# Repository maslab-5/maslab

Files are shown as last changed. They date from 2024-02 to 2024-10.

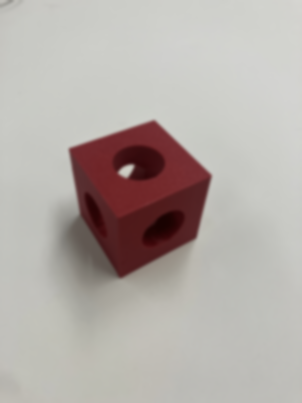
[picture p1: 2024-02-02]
nuc/vision/img/blur.png

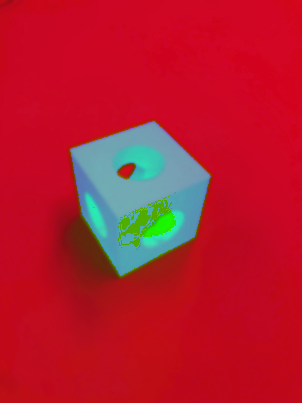
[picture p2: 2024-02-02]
nuc/vision/img/hsv.png

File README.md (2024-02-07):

# MASLAB Robot
MIT Mobile Autonomous Systems Laboratory (MASLAB) Robotics Competition – Team 5 [\[website\]](https://maslab.mit.edu/2024/wiki/team05)
<br>
Monolithic repository containing all codes and files: cad, pcb, stm32 (c), nuc (python/cv), web
<br>
<br>
1st place winner of the 2024 competition, held during IAP on February 2nd. 
<br>
Developed by Miguel Flores-Acton, Anshul Gupta, and Andy Yu

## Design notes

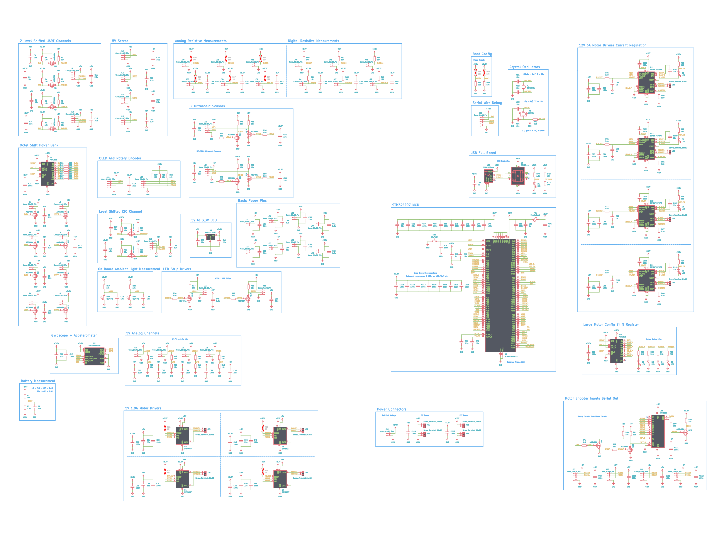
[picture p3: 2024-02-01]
web/resources/Jan_1-2/Schematic.png

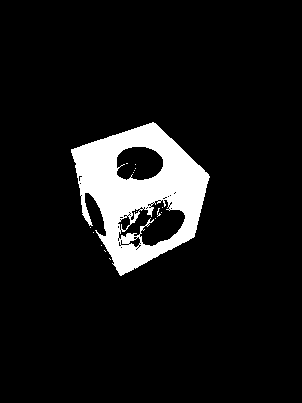
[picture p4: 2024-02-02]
nuc/vision/img/cmask.png

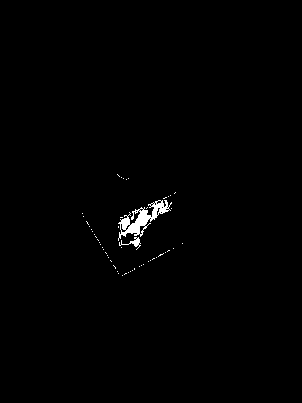
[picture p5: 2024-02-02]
nuc/vision/img/mask1.png

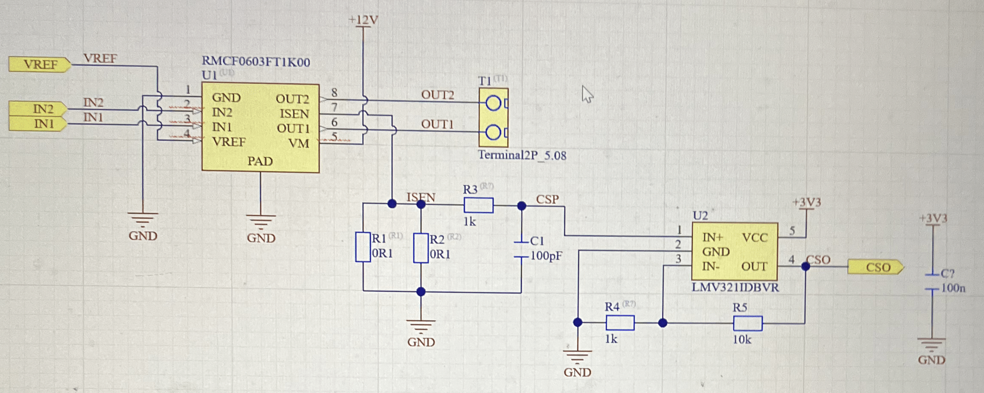
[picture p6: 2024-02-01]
web/resources/Dec_27-31/Altium.png

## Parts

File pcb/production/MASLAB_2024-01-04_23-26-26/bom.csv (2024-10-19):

Designator | Footprint | Quantity | Value | LCSC Part #
C10, C11, C14, C15, C19, C26, C27, C28, C29, C33, C35, C40, C50, C51, C52, C56, C57, C58, C59, C61, C62, C66, C68, C7, C8, C83, C85, C9 | 0603 | 28 | 2.2u
C100, C101, C102, C103, C104, C105, C110, C111, C112, C113, C114, C115, C12, C120, C121, C2, C20, C21, C22, C30, C31, C32, C34, C38, C43, C44, C48, C49, C71, C73, C74, C76, C80, C81, C84, C86, C88, C89 | 0402 | 38 | 100n
C106, C107, C108, C109, C78, C87, C94, C95 | 0402 | 8 | 1u
C116, C117, C118, C119 | 0402 | 4 | 22n
C13, C69, C77, C96, C97, C98 | C_Elec_8x6.2 | 6 | 100u
C18, C23, C39, C47, C53, C6 | 0402 | 6 | 4.7n
C24, C25, C37, C41, C42, C45, C46 | 0805 | 7 | 22u
C90, C91 | 0402 | 2 | 15p
C92, C93 | 0402 | 2 | 10p
C99 | C_Elec_8x6.2 | 1 | 100u | C178539
D1, D10, D11, D2, D3, D4, D5, D6, D7, D8, D9 | 0603 | 11 | LED
FB1 | 0805 | 1 | FerriteBead
J56 | USB_Micro-B_Molex-105017-0001 | 1 | USB_B_Micro
Q1, Q10, Q11, Q12, Q13, Q14, Q15, Q18, Q19, Q2, Q20, Q21, Q22, Q3, Q4, Q5, Q7, Q9 | SOT-23 | 18 | AO3400A
R1, R10, R11, R12, R23, R24, R27, R28, R30, R31, R32, R35, R37, R39, R43, R45, R5, R51, R52, R53, R54, R55, R62, R63, R64, R65, R66, R67, R7, R74, R75, R82, R83, R9, R97 | 0402 | 35 | 10k
R100, R101, R102, R103, R13, R14, R15, R16, R17, R18, R19, R2, R20, R3, R38, R4, R50, R60, R61, R72, R73, R76, R77, R78, R79, R80, R81, R84, R85, R86, R87, R88, R89, R90, R91, R93, R94, R95, R96, R98, R99 | 0402 | 41 | 510
R29, R36, R42, R44, R46, R47, R6, R8, R92 | 0402 | 9 | 5.1k
SW1 | SW_SPST_TL3342 | 1 | SW_Push
U1, U10 | SOIC-16_3.9x9.9mm_P1.27mm | 2 | 74HC595
U11, U12, U13, U14 | HTSSOP-16-1EP_4.4x5mm_P0.65mm_EP3.4x5mm_Mask2.46x2.31mm | 4 | DRV8874PWPR
U15 | SOIC-16_3.9x9.9mm_P1.27mm | 1 | 74HC165
U2 | LGA-14_3x2.5mm_P0.5mm_LayoutBorder3x4y | 1 | ICM-42670-P
U3, U4, U6, U7 | WSON-8-1EP_2x2mm_P0.5mm_EP0.9x1.6mm | 4 | DRV8837
U5 | SOT-223-3_TabPin2 | 1 | AMS1117-3.3
U8 | LQFP-100_14x14mm_P0.5mm | 1 | STM32F407VETx
U9 | SOT-23-6 | 1 | SRV05-4
Y1 | Crystal_SMD_3215-2Pin_3.2x1.5mm | 1 | 32.768kHz
Y2 | Crystal_SMD_3225-4Pin_3.2x2.5mm | 1 | 16MHz

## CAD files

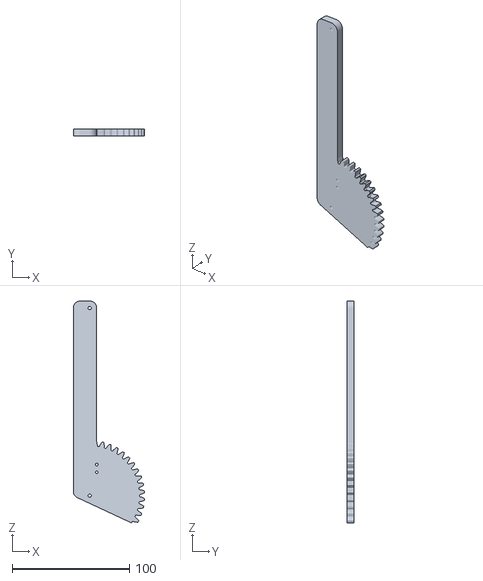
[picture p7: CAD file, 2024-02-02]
cad/parts/GearBar.stl
60.9 x 6.35 x 189.3

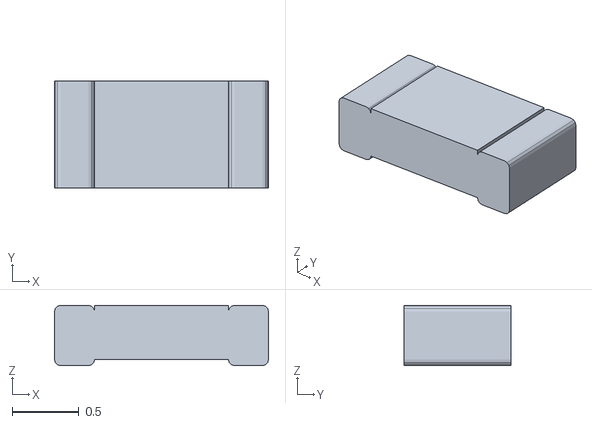
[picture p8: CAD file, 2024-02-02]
cad/parts/SOLID (16).stl
1.60 x 0.8 x 0.45

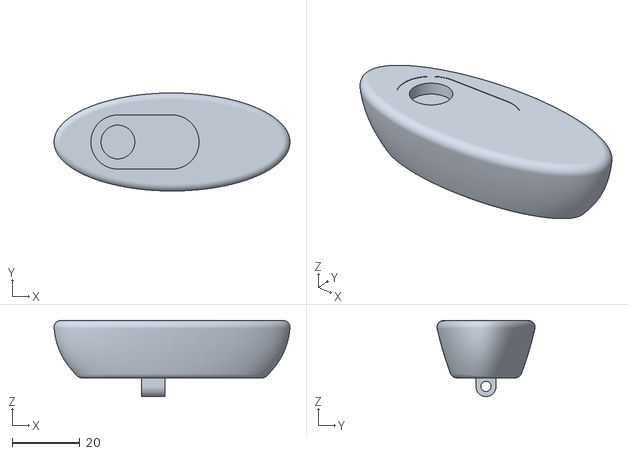
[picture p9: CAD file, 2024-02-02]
cad/parts/Camera.stl
69.8 x 29.0 x 22.5

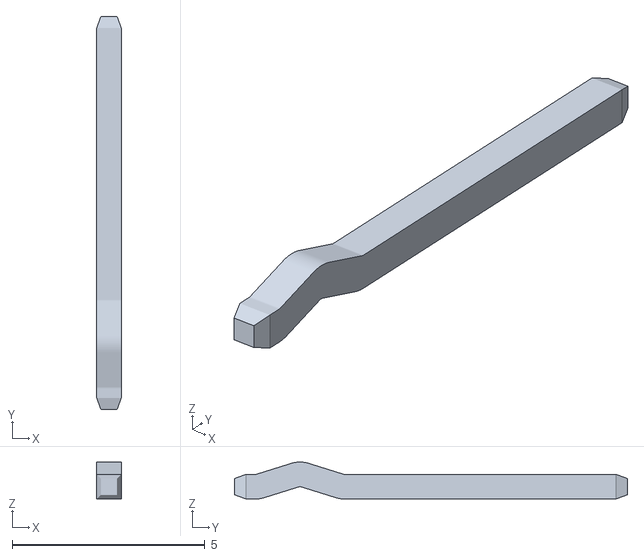
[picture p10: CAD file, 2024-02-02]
cad/parts/COMPOUND (11).stl
0.64 x 10.2 x 0.96

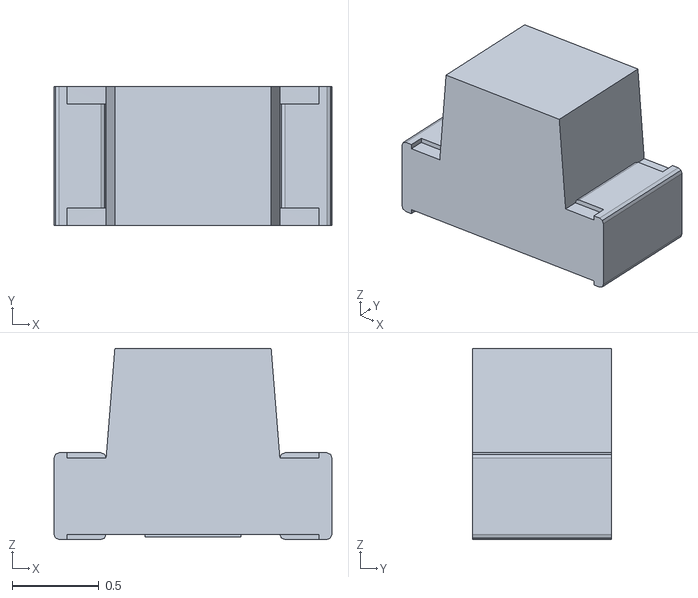
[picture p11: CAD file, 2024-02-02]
cad/parts/SOLID (14).stl
1.60 x 0.8 x 1.10

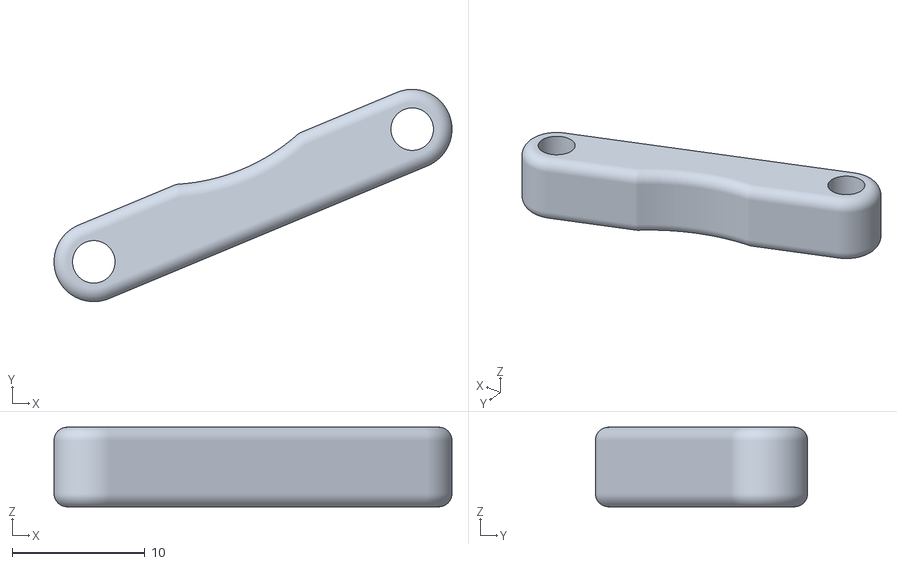
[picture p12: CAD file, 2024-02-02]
cad/parts/FenceLink.stl
30.0 x 16.0 x 6.00

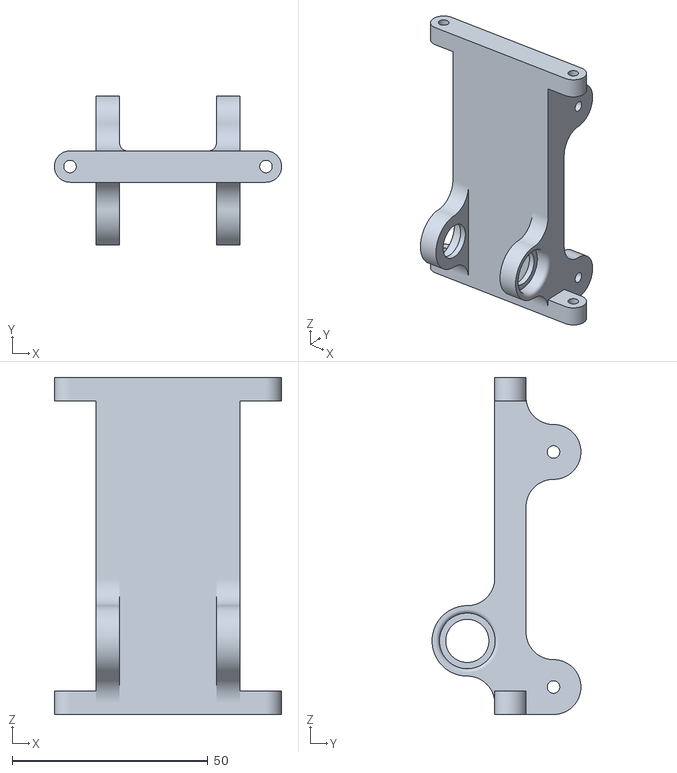
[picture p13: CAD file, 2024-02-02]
cad/parts/BarMount.stl
58.0 x 38.0 x 86.0

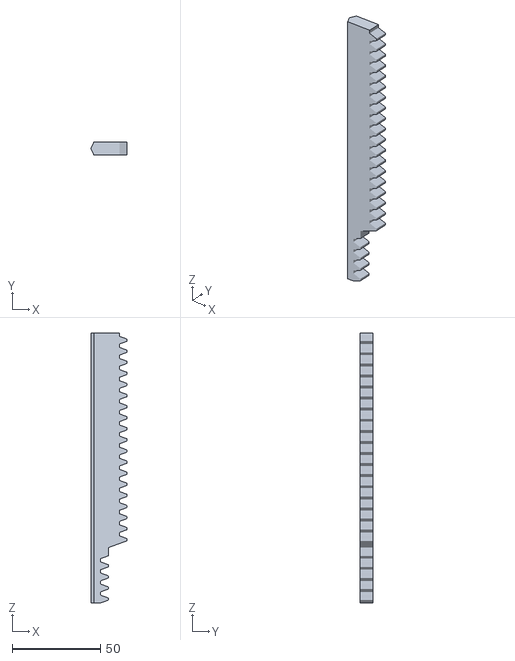
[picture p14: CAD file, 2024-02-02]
cad/parts/Rack.stl
20.6 x 7.40 x 153.0

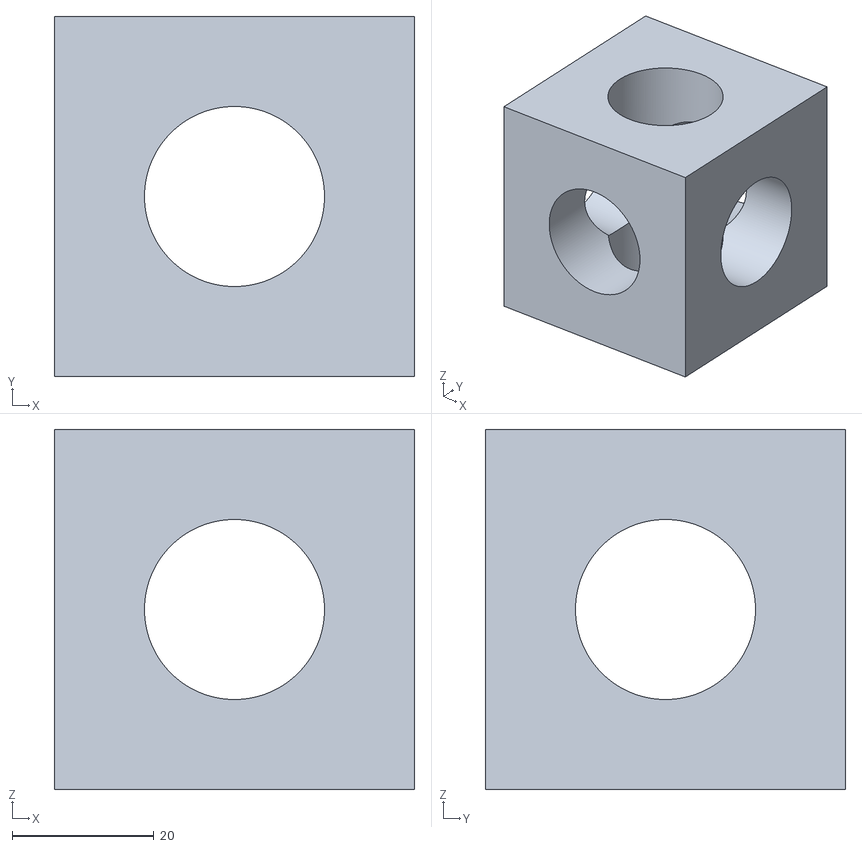
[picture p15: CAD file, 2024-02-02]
cad/parts/Cube.stl
50.8 x 50.8 x 50.8

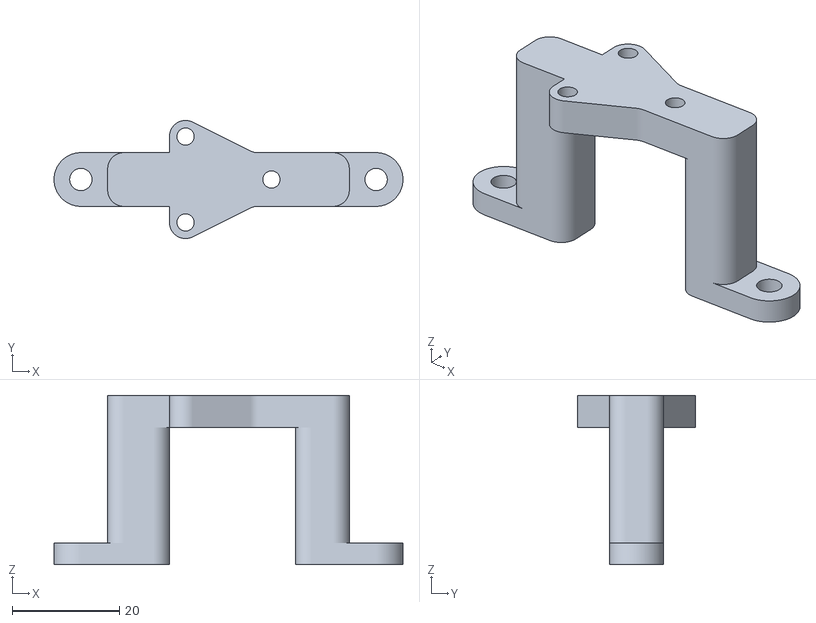
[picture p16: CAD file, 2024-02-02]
cad/parts/RollerMount.stl
65.0 x 22.0 x 31.5

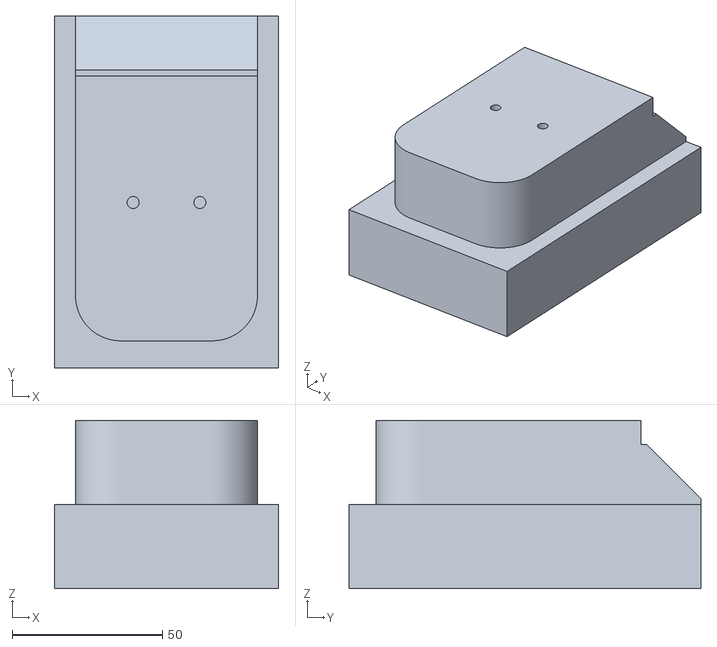
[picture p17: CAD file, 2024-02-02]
cad/parts/Battery.stl
74.5 x 117.0 x 56.0

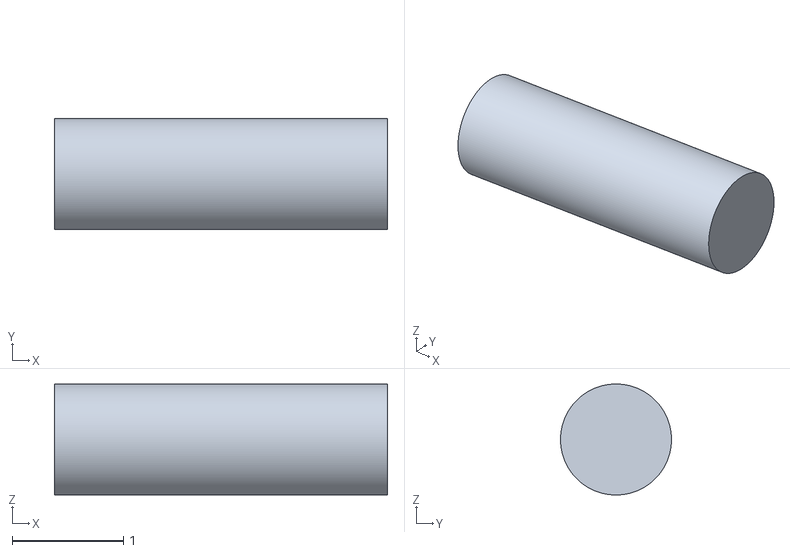
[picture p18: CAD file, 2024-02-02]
cad/parts/WirePlus.stl
3.00 x 1.00 x 1

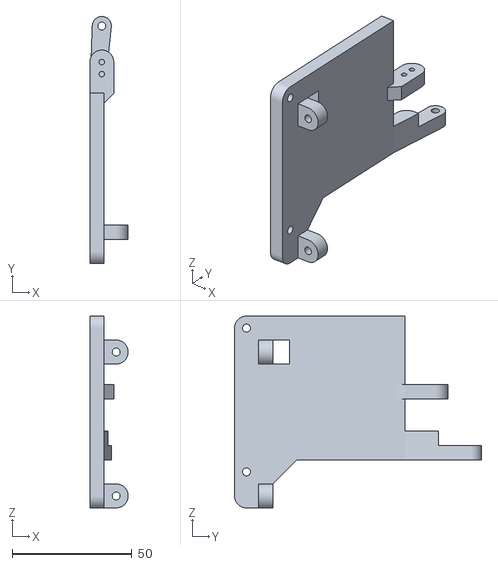
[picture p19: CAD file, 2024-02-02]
cad/parts/GateMountRight.stl
16.0 x 103.0 x 80.0

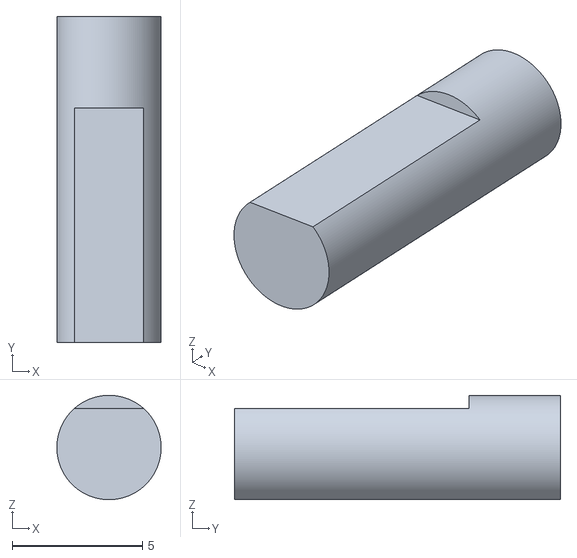
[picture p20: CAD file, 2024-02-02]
cad/parts/Axle.stl
4.00 x 12.5 x 4.00

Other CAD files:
cad/parts/SOLID (19).stl
cad/parts/CameraBar.stl
cad/parts/BottomSpacer.stl
cad/parts/Lifter.stl
cad/parts/Arm.stl
cad/parts/Axle (1).stl
cad/parts/BackBar.stl
cad/parts/BackPillar.stl
cad/parts/Ball.stl
cad/parts/BarMountSopport.stl
cad/parts/Bearing.stl
cad/parts/BearingMount.stl
cad/parts/BoardSpacer.stl
cad/parts/Body.stl
cad/parts/Bottom.stl
cad/parts/COMPOUND (1).stl
cad/parts/COMPOUND (10).stl
cad/parts/COMPOUND (12).stl
cad/parts/COMPOUND (13).stl
cad/parts/COMPOUND (14).stl
cad/parts/COMPOUND (15).stl
cad/parts/COMPOUND (16).stl
cad/parts/COMPOUND (17).stl
cad/parts/COMPOUND (18).stl
cad/parts/COMPOUND (19).stl
cad/parts/COMPOUND (2).stl
cad/parts/COMPOUND (20).stl
cad/parts/COMPOUND (21).stl
cad/parts/COMPOUND (22).stl
cad/parts/COMPOUND (23).stl
cad/parts/COMPOUND (24).stl
cad/parts/COMPOUND (3).stl
cad/parts/COMPOUND (4).stl
cad/parts/COMPOUND (5).stl
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

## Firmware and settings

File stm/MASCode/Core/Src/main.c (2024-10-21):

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
/* Includes ------------------------------------------------------------------*/
#include "main.h"
#include "usb_device.h"

/* USER CODE BEGIN Includes */
#include "usbd_cdc_if.h"
#include "control.h"
#include "registers.h"
/* USER CODE END Includes */

ADC_HandleTypeDef hadc1;
ADC_HandleTypeDef hadc2;
ADC_HandleTypeDef hadc3;

I2C_HandleTypeDef hi2c1;
I2C_HandleTypeDef hi2c3;

SPI_HandleTypeDef hspi3;

TIM_HandleTypeDef htim1;
TIM_HandleTypeDef htim2;
TIM_HandleTypeDef htim3;
TIM_HandleTypeDef htim4;
TIM_HandleTypeDef htim5;
TIM_HandleTypeDef htim7;
TIM_HandleTypeDef htim9;
TIM_HandleTypeDef htim10;
TIM_HandleTypeDef htim11;
TIM_HandleTypeDef htim12;

UART_HandleTypeDef huart2;
UART_HandleTypeDef huart6;

void SystemClock_Config(void);
static void MX_GPIO_Init(void);
static void MX_ADC1_Init(void);
static void MX_I2C1_Init(void);
static void MX_I2C3_Init(void);
static void MX_SPI3_Init(void);
static void MX_TIM1_Init(void);
static void MX_TIM2_Init(void);
static void MX_TIM3_Init(void);
static void MX_TIM4_Init(void);
static void MX_TIM9_Init(void);
static void MX_TIM10_Init(void);
static void MX_TIM11_Init(void);
static void MX_TIM12_Init(void);
static void MX_USART2_UART_Init(void);
static void MX_USART6_UART_Init(void);
static void MX_ADC2_Init(void);
static void MX_ADC3_Init(void);
static void MX_TIM5_Init(void);
static void MX_TIM7_Init(void);
/**
  * @brief  The application entry point.
  * @retval int
  */
int main(void)
{
  /* MCU Configuration--------------------------------------------------------*/

  /* Reset of all peripherals, Initializes the Flash interface and the Systick. */
  HAL_Init();

  /* Configure the system clock */
  SystemClock_Config();

  /* Initialize all configured peripherals */
  MX_GPIO_Init();
  MX_ADC1_Init();
  MX_I2C1_Init();
  MX_I2C3_Init();
  MX_SPI3_Init();
  MX_TIM1_Init();
  MX_TIM2_Init();
  MX_TIM3_Init();
  MX_TIM4_Init();
  MX_TIM9_Init();
  MX_TIM10_Init();
  MX_TIM11_Init();
  MX_TIM12_Init();
  MX_USART2_UART_Init();
  MX_USART6_UART_Init();
  MX_ADC2_Init();
  MX_ADC3_Init();
  MX_USB_DEVICE_Init();
  MX_TIM5_Init();
  MX_TIM7_Init();
  /* USER CODE BEGIN 2 */
	HAL_Delay(10);

	Control_Init();

	HAL_Delay(10);
  /* USER CODE END 2 */

  /* Infinite loop */
  /* USER CODE BEGIN WHILE */
	while (1) {
		Control_Loop();
    /* USER CODE END WHILE */

    /* USER CODE BEGIN 3 */
	}
  /* USER CODE END 3 */
}

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
/* USER CODE BEGIN 4 */
void HAL_TIM_PeriodElapsedCallback(TIM_HandleTypeDef *htim) {
	if (htim == &htim5) {
		registerHandler();
	} else { //Timer 7 for digital read of UI

	}
}
/* USER CODE END 4 */
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


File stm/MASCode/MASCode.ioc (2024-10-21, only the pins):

Mcu.UserName=STM32F407VETx
PA0-WKUP.GPIO_Label=AIN3
PA0-WKUP.Signal=ADCx_IN0
PA1.GPIO_Label=RM1
PA1.Signal=ADCx_IN1
PA10.GPIO_Label=DRESW
PA10.Signal=GPIO_Input
PA11.Signal=USB_OTG_FS_DM
PA12.Signal=USB_OTG_FS_DP
PA13.Signal=SYS_JTMS-SWDIO
PA14.Signal=SYS_JTCK-SWCLK
PA15.GPIO_Label=GCS
PA15.Signal=GPIO_Output
PA2.GPIO_Label=RM2
PA2.Signal=ADCx_IN2
PA3.GPIO_Label=RM3
PA3.Signal=ADCx_IN3
PA4.GPIO_Label=RM6
PA4.Signal=ADCx_IN4
PA5.GPIO_Label=RM5
PA5.Signal=ADCx_IN5
PA6.GPIO_Label=RM4
PA6.Signal=ADCx_IN6
PA7.GPIO_Label=BREF
PA7.Signal=ADCx_IN7
PA8.GPIO_Label=SCL2
PA8.Signal=I2C3_SCL
PA9.Signal=USB_OTG_FS_VBUS
PB0.GPIO_Label=M1EN
PB0.Signal=S_TIM3_CH3
PB1.GPIO_Label=M1REF
PB1.Signal=S_TIM3_CH4
PB10.GPIO_Label=M5IN1
PB10.Signal=S_TIM2_CH3
PB11.GPIO_Label=M5IN2
PB11.Signal=S_TIM2_CH4
PB12.GPIO_Label=STRP2
PB12.Signal=GPIO_Output
PB13.GPIO_Label=STRP1
PB13.Signal=GPIO_Output
PB14.GPIO_Label=M6IN1
PB14.Signal=S_TIM12_CH1
PB15.GPIO_Label=M6IN2
PB15.Signal=S_TIM12_CH2
PB2.GPIO_Label=BOOT1
PB2.Signal=GPIO_Input
PB3.Signal=SYS_JTDO-SWO
PB4.GPIO_Label=M4EN
PB4.Signal=S_TIM3_CH1
PB5.GPIO_Label=M4REF
PB5.Signal=S_TIM3_CH2
PB6.GPIO_Label=SCL1
PB6.Signal=I2C1_SCL
PB7.GPIO_Label=SDA1
PB7.Signal=I2C1_SDA
PB8.GPIO_Label=M3EN
PB8.Signal=S_TIM10_CH1
PB9.GPIO_Label=M3REF
PB9.Signal=S_TIM11_CH1
PC0.GPIO_Label=AMB2
PC0.Signal=ADCx_IN10
PC1.GPIO_Label=AIN4
PC1.Signal=ADCx_IN11
PC10.GPIO_Label=GSCK
PC10.Signal=SPI3_SCK
PC11.GPIO_Label=GMISO
PC11.Signal=SPI3_MISO
PC12.GPIO_Label=GMOSI
PC12.Signal=SPI3_MOSI
PC13-ANTI_TAMP.GPIO_Label=TRIG1
PC13-ANTI_TAMP.Signal=GPIO_Output
PC14-OSC32_IN.Signal=RCC_OSC32_IN
PC15-OSC32_OUT.Signal=RCC_OSC32_OUT
PC2.GPIO_Label=AIN2
PC2.Signal=ADCx_IN12
PC3.GPIO_Label=AIN1
PC3.Signal=ADCx_IN13
PC4.GPIO_Label=AMB1
PC4.Signal=ADCx_IN14
PC5.GPIO_Label=LMDAT
PC5.Signal=GPIO_Output
PC6.GPIO_Label=TX2
PC6.Signal=USART6_TX
PC7.GPIO_Label=RX2
PC7.Signal=USART6_RX
PC8.GPIO_Label=DRE2
PC8.Signal=GPIO_Input
PC9.GPIO_Label=SDA2
PC9.Signal=I2C3_SDA
PD0.GPIO_Label=GINT2
PD0.Signal=GPXTI0
PD1.GPIO_Label=GINT1
PD1.Signal=GPXTI1
PD10.GPIO_Label=SRCLK
PD10.Signal=GPIO_Output
PD11.GPIO_Label=DRE1
PD11.Signal=GPIO_Input
PD12.GPIO_Label=M7IN1
PD12.Signal=S_TIM4_CH1
PD13.GPIO_Label=M7IN2
PD13.Signal=S_TIM4_CH2
PD14.GPIO_Label=M8IN1
PD14.Signal=S_TIM4_CH3
PD15.GPIO_Label=M8IN2
PD15.Signal=S_TIM4_CH4
PD2.GPIO_Label=RMD7
PD2.Signal=GPIO_Input
PD3.GPIO_Label=RMD8
PD3.Signal=GPIO_Input
PD4.GPIO_Label=RMD9
PD4.Signal=GPIO_Input
PD5.GPIO_Label=TX1
PD5.Signal=USART2_TX
PD6.GPIO_Label=RX1
PD6.Signal=USART2_RX
PD7.GPIO_Label=RMD10
PD7.Signal=GPIO_Input
PD8.GPIO_Label=SRDAT
PD8.Signal=GPIO_Output
PD9.GPIO_Label=SRSV
PD9.Signal=GPIO_Output
PE0.GPIO_Label=RMD11
PE0.Signal=GPIO_Input
PE1.GPIO_Label=RMD12
PE1.Signal=GPIO_Input
PE10.GPIO_Label=ENSO
PE10.Signal=GPIO_Input
PE11.GPIO_Label=SRV2
PE11.Signal=S_TIM1_CH2
PE12.GPIO_Label=ENPL
PE12.Signal=GPIO_Output
PE13.GPIO_Label=SRV3
PE13.Signal=S_TIM1_CH3
PE14.GPIO_Label=SRV4
PE14.Signal=S_TIM1_CH4
PE15.GPIO_Label=ENCLK
PE15.Signal=GPIO_Output
PE2.GPIO_Label=TRIG2
PE2.Signal=GPIO_Output
PE3.GPIO_Label=ECHO2
PE3.Signal=GPIO_Input
PE4.GPIO_Label=ECHO1
PE4.Signal=GPIO_Input
PE5.GPIO_Label=M2EN
PE5.Signal=S_TIM9_CH1
PE6.GPIO_Label=M2REF
PE6.Signal=S_TIM9_CH2
PE7.GPIO_Label=LMSV
PE7.Signal=GPIO_Output
PE8.GPIO_Label=LMCLK
PE8.Signal=GPIO_Output
PE9.GPIO_Label=SRV1
PE9.Signal=S_TIM1_CH1
PH0-OSC_IN.Signal=RCC_OSC_IN
PH1-OSC_OUT.Signal=RCC_OSC_OUT

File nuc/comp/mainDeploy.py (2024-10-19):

from map import Map
from camera import Camera
from command import Com, SmallMotor, LargeMotor, Servo, Switch, Movement
from actions import Actions
from visual import Visual

import math
import time
import os

# updating code
# git add .
# git commit -m "message"
# git push

# getting code
# cd robot/nuc-data
# git pull

running_nuc = os.name != 'nt'

preBlur = 9
postBlur = 7
resizeWidth = 256
resizeHeight = 192

green_range = [[40, 17, 17], [100, 255, 255]]
red_range = [[-10, 20, 20], [10, 255, 255]]

unitLength = 1462
unitRotation = 1575

camera_bias_x = -8

roughStartX = 2
roughStartY = 1

stackOrder = [2, 4, 3, 1, 0]

maxLoop = 24
dropTime = 150

map = Map("mapright.txt", roughStartX, roughStartY)
camera = Camera(running_nuc, resizeWidth, resizeHeight, preBlur, postBlur)
command = Com(115200)
visual = Visual(camera, camera_bias_x, green_range, red_range)
act = Actions(map, command, visual, unitLength, unitRotation, maxLoop, dropTime)

def init():
    command.startGyroCal(3000)
    while not command.isGyroCal():
        time.sleep(1/maxLoop)

    command.setPosition(map.roughStartX*unitLength, map.roughStartY*unitLength, map.startAng)

    command.setMotorEnable(LargeMotor.Lift, 1)
    command.setMotorDirection(LargeMotor.Lift, 0)
    command.setMotorCurrent(LargeMotor.Lift, 48)
    command.setMotorEnable(LargeMotor.Chute, 1)
    command.setMotorDirection(LargeMotor.Chute, 1)
    command.setMotorCurrent(LargeMotor.Chute, 100)

    command.setParameters(0.6, 0.00075)

    command.moveServo(Servo.Camera, 275)
    command.moveServo(Servo.Gate, 310)
    command.moveServo(Servo.LeftChute, 35)
    command.moveServo(Servo.RightChute, 528)

    command.motorMove(SmallMotor.Gate, 0, 100)
    command.setMotorSpeed(LargeMotor.Lift, 50)
    command.setMotorSpeed(LargeMotor.Chute, 100)

    time.sleep(1.5)

    command.motorMove(SmallMotor.Gate, 0, 0)
    command.setMotorDirection(LargeMotor.Chute, 0)
    command.setMotorDirection(LargeMotor.Lift, 0)

    time.sleep(0.25)

    command.setMotorEnable(LargeMotor.Lift, 0)
    command.setMotorSpeed(LargeMotor.Lift, 0)

    while not command.getSwitch(Switch.ChuteLimit):
        time.sleep(1/maxLoop)

    command.setMotorSpeed(LargeMotor.Chute, 0)
    command.setMotorDirection(LargeMotor.Chute, 1)


init()

# act.turnToStack(Movement.Spin, stackOrder[0])
# act.moveUptoStack(stackOrder[0])
# act.alignCamera()
# act.grabStack(stackOrder[0])
# act.turnToBearingNearest(Movement.Spin, -3*math.pi/4)
# act.sortStack()

# act.turnToPositionNearest(Movement.Spin, 2, 2)
# act.moveToPosition(2, 2, 1)
# act.turnToStack(Movement.Spin, stackOrder[1])
# act.moveUptoStack(stackOrder[1])
# act.alignCamera()
# act.grabStack(stackOrder[1])
# act.turnToBearingNearest(Movement.Spin, math.pi/2)
# act.sortStack()

# act.turnToPositionNearest(Movement.Spin, 2, 0.9)
# act.moveToPosition(2, 0.9, 1)
# act.turnToStack(Movement.Spin, stackOrder[2])
# act.moveUptoStack(stackOrder[2])
# act.alignCamera()
# act.grabStack(stackOrder[2])
# act.turnToBearingNearest(Movement.Spin, math.pi/2)
# act.sortStack()

# act.turnToPositionNearest(Movement.Spin, 2, 2)
# act.moveToPosition(2, 2, 1)
# act.turnToStack(Movement.Spin,stackOrder[3])
# act.moveUptoStack(stackOrder[3])
# act.alignCamera()
# act.grabStack(stackOrder[3])
# act.turnToBearingNearest(Movement.Spin, 0)
# act.sortStack()

# act.turnToPositionNearest(Movement.Spin, 1, 3)
# act.moveToPosition(1, 3, 1)
# act.turnToStack(Movement.Spin, stackOrder[4])
# act.moveUptoStack(stackOrder[4])
# act.alignCamera()
# act.grabStack(stackOrder[4])
# act.turnToBearingNearest(Movement.Spin, 0)
# act.sortStack()


act.turnToPositionNearest(Movement.Spin, 1, 1)
act.moveToPosition(1, 1, 1)
act.turnToBearingNearest(Movement.Spin, math.pi/2)
act.dropGround()

act.turnToPositionNearest(Movement.Spin, 1.5, 2.6)
act.moveToPosition(1.5, 2.6, 1)
act.turnToBearingNearest(Movement.Spin, 0)
# act.waitDrop()
act.dropPlatform()

camera.destroy()

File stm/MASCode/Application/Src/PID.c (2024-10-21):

#include "PID.h"
#include "encoders.h"
#include <stdlib.h>
#include "math.h"
#include "timer.h"

//kd -> enc/ms
//ki -> enc*ms
static float kp, ki, kd;//2, 0.00005, 200
static uint8_t maxSignal;//80

static int32_t errPrev[2] = {0};
static int32_t errInt[2] = {0};
static int32_t target[2] = {0};

static struct Timer timer = {0};

void initPID(float _kp, float _ki, float _kd, uint8_t maxSig) {
	kp = _kp;
	ki = _ki;
	kd = _kd;
	maxSignal = maxSig;
}

void resetPID(void) {
	for (uint8_t motor = 0; motor < 2; motor++) {
		errPrev[motor] = 0;
		errInt[motor] = 0;
	}
}

void updatePID(void) {
	updateTimer(&timer);
	if (!timerReady(&timer)) {
		return;
	}
	//sample encoders at same time
	const int32_t pos[2] = {getEncoder(LeftMotor), getEncoder(RightMotor)};

	uint8_t dir[2] = {0};
	uint8_t speed[2] = {0};

	for (uint8_t motor = 0; motor < 2; motor++) {
		const int32_t err = pos[motor] - target[motor];

		errInt[motor] += err*timer.deltaTime;
		const float drive = kp*(float)err + kd*(float)(err - errPrev[motor])/(float)timer.deltaTime + ki*(float)errInt[motor];
		errPrev[motor] = err;

		dir[motor] = drive > 0;
		speed[motor] = fmin(fabs(drive), maxSignal);
	}

	//write motor speeds at same time
	for (uint8_t motor = 0; motor < 2; motor++) {
		largeMotorDirection(motor, dir[motor]);
		largeMotorSpeed(motor, speed[motor]);
	}
}

void setTarget(enum LargeMotor motor, int32_t trgt) {
	target[motor] = trgt;
}

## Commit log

2024-10-19 Update pcb files
    [MASLAB.kicad_sch, bom.csv, designators.csv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]
2024-10-19 Rename pcb files
    [maslab.kicad_sch]
2024-10-19 Remove backups and old production files
    [bom.csv, designators.csv, positions.csv]
2024-10-23 Ignore kicad backups

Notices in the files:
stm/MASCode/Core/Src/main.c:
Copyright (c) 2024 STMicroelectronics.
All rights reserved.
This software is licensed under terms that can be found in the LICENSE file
